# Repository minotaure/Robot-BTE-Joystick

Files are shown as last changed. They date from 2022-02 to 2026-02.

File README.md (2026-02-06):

# Robot-BTE-Joystick
Robot Mélia de découverte pour l'Ecole des Mines de Paris et classes de 3ème

## Participants au projet (ordre alphabétique):
Maxime CHUREAU\
Remy MARTINEZ\
Naimeric VILLAFRUELA

## Versions des robots
2 versions sont disponibles :
* Une version du robot contrôlable via une interface WEB via du WIFI (robot-version-wifi)
* Une autre contrôlable via un joystick Bluetooth (robot-version-BT)

## Les fichiers

- BOM (contient les listes de matériels pour fabriquer les robots)

- robot-version-BT (contient la bersion Bluetooth)
    - Code (contient le code pour le robot et la télécomande)
    - Electronique (contient le schéma fritzing et un jpg du schéma)

[Attention : La version robot-version-BT n'est pas complètement fonctionnelle. Seule la version contenue dans robot-v-finale est fonctionnelle]
    
- robot-version-wifi (contient la version Wifi)

- Structure (contient les fichiers de la structure du robot (identique pour les deux))
    - STLs (contient les pièces à imprimer pour sur-élever la bille avant et fixer les moteurs)
    - SVGs (contient le schéma de la plateforme à découper au laser)

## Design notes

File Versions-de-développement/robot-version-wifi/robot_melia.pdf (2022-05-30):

# Le robot Mélia

### Rémy Martinez - Cahier Vert 2022

## Table des matières

1 Introduction | 2
2 Le robot | 2
3 Montage | 2
4 Pistes d’amélioration | 5

1

## 1 Introduction

Le montage du robot est une des activités proposées par le pôle Mélia de Cahier Vert. L’idée est de permettre une introduction de problématiques d’ingéniérie auprès d’élèves de 3e au travers du montage d’un petit robot. Ce document vise à être une sorte de mode d’emploi complet des fonctionnalités du robot et de son montage (à l’issue du mandat 2021-2022).

## 2 Le robot

Le robot étant un support pédagogique adressé aux collégiens, il doit attirer leur attention tout en étant "sobre" d’un point de vue du matériel. Le choix a donc été fait de concevoir un robot roulant, avec deux roues motrices et une roue libre. Le tout se base sur une architecture composée d’un arduino et d’un hacheur.

## 3 Montage

### 3.1 Le matériel

### 3.1.1 L’arduino

Le design retenu en 2022 se base sur un arduino nano capable d’être l’hote d’un réseau wifi. Plusieurs modèles peuvent faire l’affaite : nano iot 33, bte, ou RP2040. De par les capteurs pré-intégrés (accéléromètre, LED RGB, micro ...) et dans une optique de futures améliorations nous avons choisi les RP2040. Il en faut un par robot et c’est lui qui gère toute la partie commande.
[insérer image d’un arduino]
Attention : Il peut être alimenté via du micro USB ou directement sur le pin VIN (allez voir dans la doc lequel c’est, ce pin est assez tolérant en termes de tensions qu’il accepte). Cependant il est fortement déconseillé de l’alimenter par ces deux voies en même temps : il risque de griller. Attention 2 : Contrairement aux arduino "classiques" pour lesquels les niveaux logiques sont 0 et 5V, pour les arduino nano c’est 0 et 3.3V. Faites attention a être cohérent dans un même circuit pour ne pas avoir de mauvaises surprises

2

### 3.1.2 Le hacheur

Nous avons cherché un hacheur qui peut faire varier la tension (pour faire tourner les moteurs a différentes vitesses), avec 2 canaux (un par roue), qui prenne une tension logique 3.3V et qui soit le moins cher possible. Nous avons donc convergé vers les L9110 de Kitronic.
Warning : L’alimentation des hacheurs a une polarité et ils ne sont pas forcement protégés contre un mauvais branchement. Donc branchez les bien ! [insérer image d’un hacheur]

### 3.1.3 Matériel supplémentaire

Pour un robot il faut ajouter à cela : - Du contreplaqué 5mm (2 pièces à découper au laser + des cales a découper)

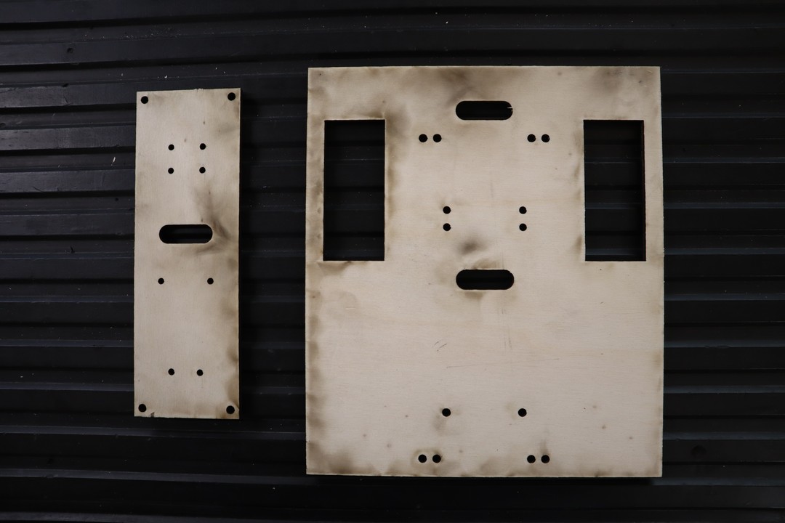
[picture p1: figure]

Figure 1 – Pièces à découper

- Deux "moteurs jaunes" + les roues qui vont avec
- Une bille porteuse (roue avant)
- une pile 9V (qui alimente la partie commande et puissance)
- une prise pour brancher sur pile 9V
- Des connecteurs JST SM mâle et femelle (3 de chaque)
- Des connecteurs de carte electronique (2 x 15 broches)
- Des vis : 8 de 15mm pour accrocher l’electronique et les equerres au châssis, 8 de 25mm pour attacher le support elec au châssis et les moteurs aux équerres, deux de 30mm (idéalement ca aurait été au moins 35mm) pour attacher la bille porteuse.
- Les écrous qui vont avec : 18 écrous
- Un bout de velcro pour coller la pile

3

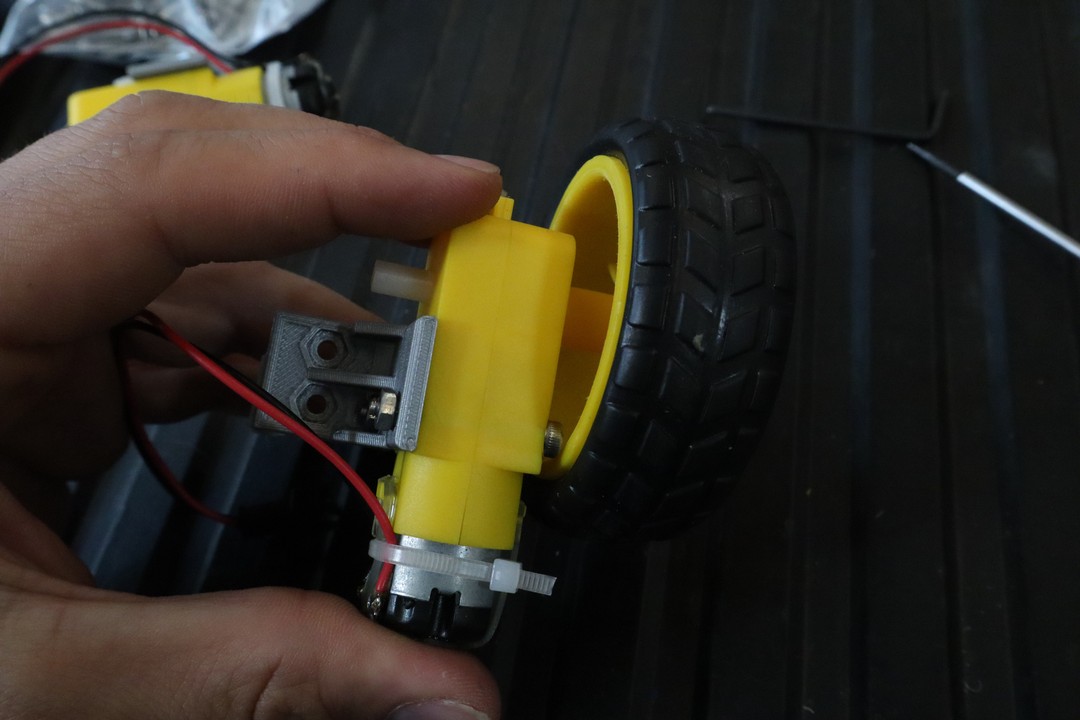
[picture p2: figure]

Figure 2 – Moteur jaune et roue (qui se rentre en force)

- Les pièces imprimées en 3D : 1 support de nano, 1 équerre gauche, 1 équerre droite
- Quelques outils

### 3.2 Instructions de montage

### 3.2.1 A faire en amont d’une session

- Découper les planches
- Soudures de l’electionique - Branchement 9V - Distribution de l’alimentation
- Fils de commande (arduino - hacheur)
- Fils en sortie du hacheur :
- Fils JST sur moteurs

### 3.2.2 Le montage

- Accorcher les moteurs sur les équerres ( Attention Equerre gauche ̸= Equerre droite)
- Accrocher l’electronique au support elec
- Accrocher Equerres sur chassis
- Accrocher bille sous chassis
- Accrocher le support elec au chassis (le faire en dernier sinon le reste ne peut plus être monté)

4

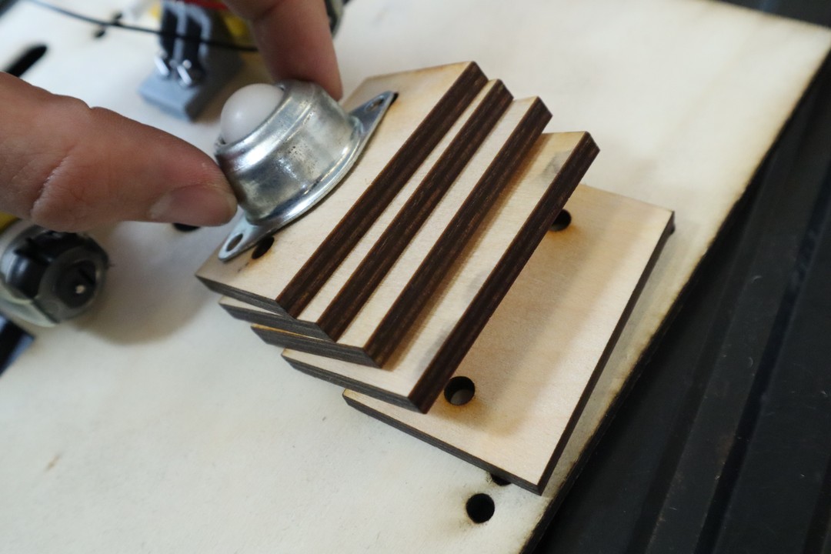
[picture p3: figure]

Figure 3 – Bille porteuse et cales

## 4 Pistes d’amélioration

- Avoir une connexion où les collégiens ne peuvent pas se planter au niveau du côté commande du hacheur
- Implémenter un joystick (il y a un code a base de websocket mais pas trouvé comment ca marche côté arduino)
- Amélioration ultime : Utiliser la centrale inertielle du RP2040 pour faire un robot en pendule inversé (faire une V2 du robot)

5

Figure 4 – Pile et velcro

Figure 5 – Support de nano imprimé en 3D

6

Figure 6 – Equerres imprimées en 3D

Figure 7 – Ecrous et clé

7

Figure 8 – Hallen et tournevis

Figure 9 – La découpe laser

8

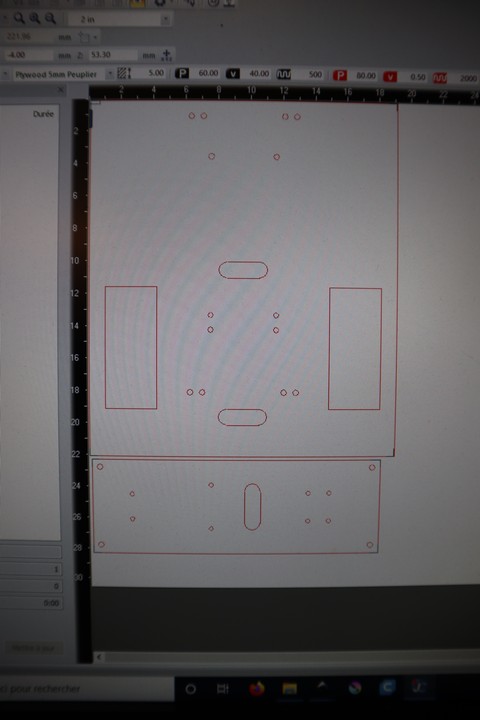
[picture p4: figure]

Figure 10 – Positionnement optimal des pièces

Figure 11 – Découpe en cours

9

Figure 12 – Fil 1 : Connexion à l’alimentation

Figure 13 – Fil 2 : Séparation en 2

10

Figure 14 – Fil 2 : Branchement des fils d’alim côté arduino

Figure 15 – Fil 2 : Zoom sur la connexion au broches de l’arduino

11

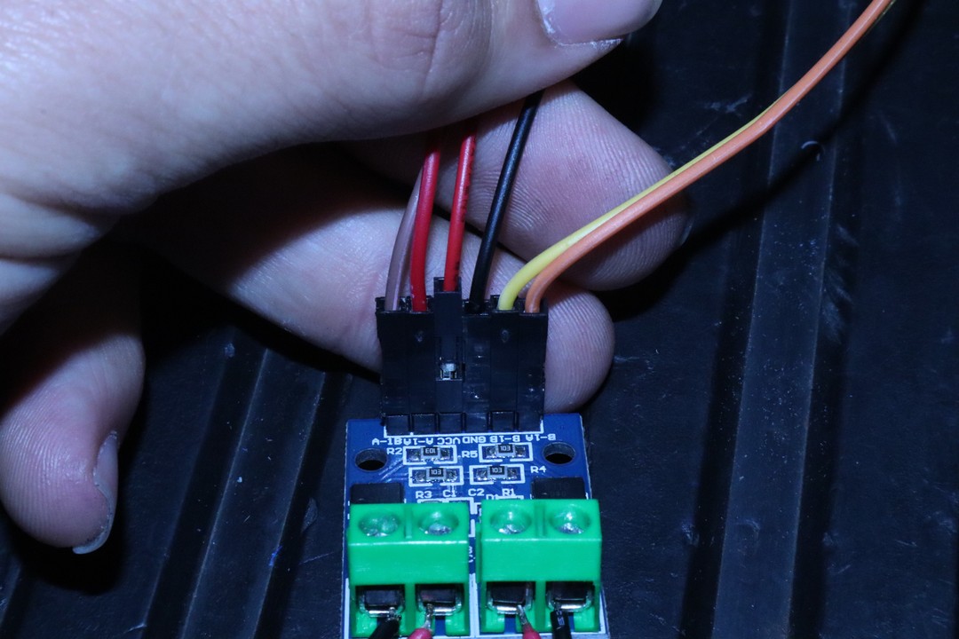
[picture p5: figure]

Figure 16 – Fil 2 : Branchement de l’alim côté hacheur (ce sont les fils rouge et noir au centre)

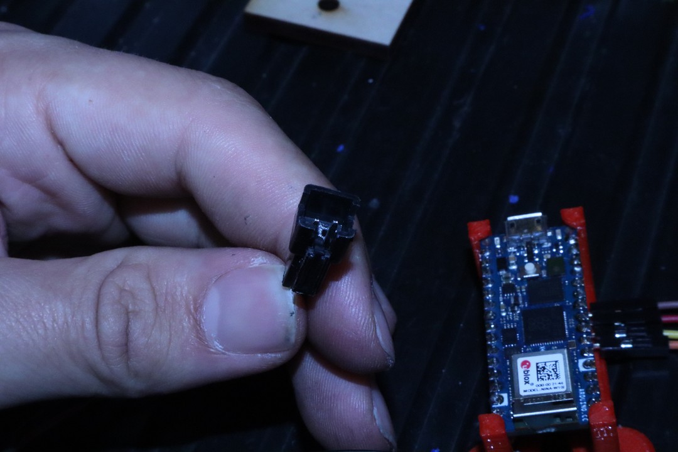
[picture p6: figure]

Figure 17 – Fil 2 : Prise JST d’alim côté arduino

12

Figure 18 – Fils 3 : Commande cpôté hacheur (les 2 fils de chaque côté)

Figure 19 – Fil 3 : Branchement de la commande côté arduino

13

Figure 20 – Fil 3 : Zoom sur la connexion aux broches de l’aduino

Figure 21 – Branchement des fils sur l’aduino (vu de dessous)

14

Figure 22 – Fils 4 : Connexion prise JST au hacheur

Figure 23 – Fils 5 : Soudure côté moteur

15

Figure 24 – Fil 5 : Prise côté moteurs

Figure 25 – Attache d’une équerre sur un moteur

16

Figure 26 – Equerres pour écrous hex.

Figure 27 – Support de l’electronique

17

Figure 28 – Moteur accroché au châssis

Figure 29 – Mise en place de la bille porteuse

18

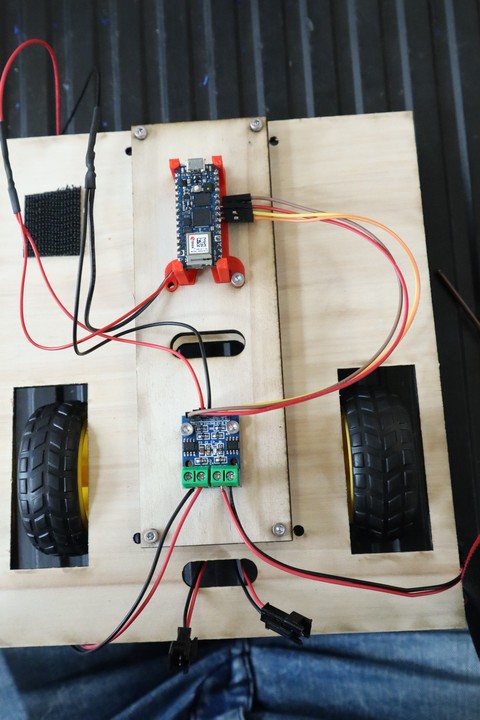
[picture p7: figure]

Figure 30 – Robot complet

19

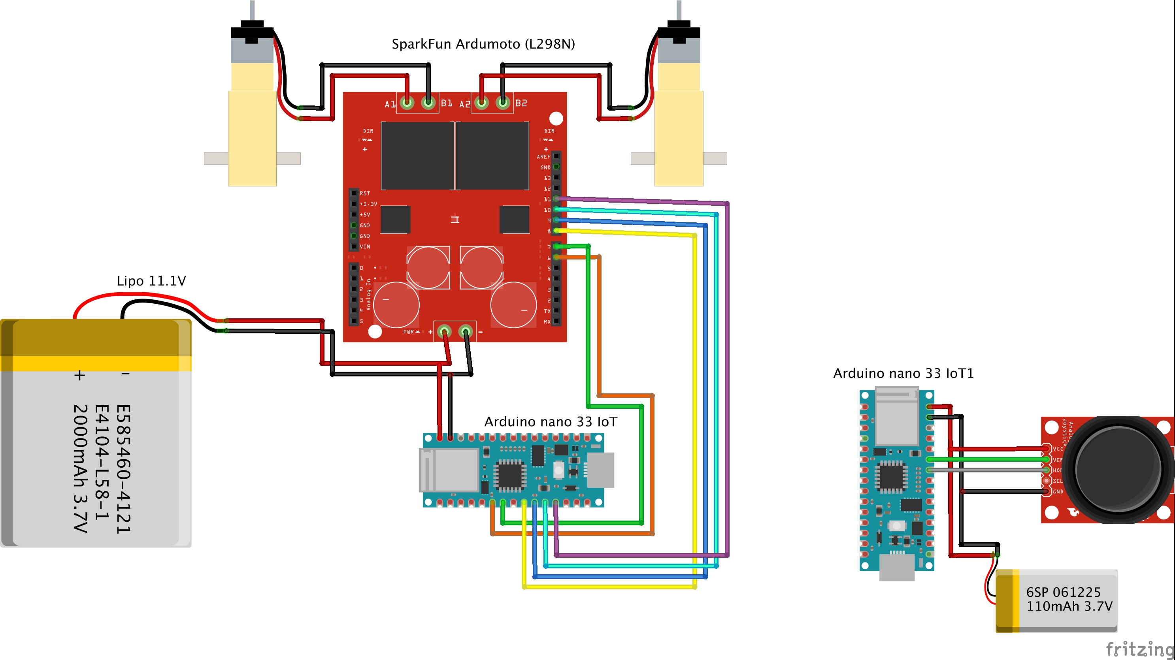
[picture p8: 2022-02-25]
Versions-de-développement/robot-version-BT/Electronique/Robot-joystick-BT.jpg

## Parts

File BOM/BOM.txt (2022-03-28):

BOM pour la version Robot + Joystick BT
##################

Arduino Nano 33 IoT : x2
Batterie Lipo 11.1V 3S : x 1
Batterie lipo 3.3V 1S : x1
Connecteur Lipo 11.1V (Femelle):  x1
Connecteur Batterie lipo 3.3V (Mµ«le+Femelle): x1
Connecteur JST 2 Pin Batterie - Arduino (Mµ«le+Femelle): x2
Connecteur JST 2 Pin Joystick - Arduino (Mµ«le+Femelle): x1
Connecteur JST 4 Pin Ardumoto-Arduino : (Mµ«le+Femelle) : x1
Moteur chinois jaunes : x2
Sparkfun Ardumoto ou identique (L298N) : x1
Joystick : x1

BOM pour la version Robot + Nano RP2040
##################

Arduino Nano RP2040 : x1
Batterie 9V 6lr61 ou Bloc Piles AA (sortie connecteur 9V) : x1
Connecteur 9V : x1
Connecteur JST SM 2 broches : x3
Connecteurs JST Femelle (pour brancher Arduino) : 2 x barres de 15 broches
Connecteurs JST Femelle (pour brancher hasheur) : 1 x barres de 6 broches
Moteur chinois jaunes : x2
Roues : x2
Carte driver moteurs 2 canaux (L9110S Kitronik) : x1
Vis CHC-M3-25 : x8 (moteur + plaque support breadboard)
Vis CHC-M4-40 : x2 (boule)
Vis CHC-M2-15 : x4 (hasheur)
Ecrous M3 : x8
Ecrous M4 : x2
Ecrous M2 : x4
Bille Porteuse : x1

Velcro autocollant
Cable ¨¦lectrique 1.5mm2 si possible de couleurs diff¨¦rentes
Piece STL pour fixer nano RP2040
(Contreplaqué 5mm)

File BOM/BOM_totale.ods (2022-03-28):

BOM pour la version Robot + Nano RP2040 |  |  |  |  |  |  |  |  |  | N | 30
 |  |  |  | Où le trouver + prix par unité |  |  |  |  |  |  |  |  |  | Prix pour N robots
 | Piècce | Qté pour 1 robot |  | RS | Prix RS | Conrad | Prix Conrad | Autre |  |  | Qté pour N robots | En stock | Qté nette à acheter | RS | Conrad | Autre
note : j’ai pris aavec les embases car a souder on a toutes les chances d’en casser au moins 1 | Arduino Nano RP2040 : x1 | 1 |  | https://fr.rs-online.com/web/p/arduino/2221486 | 27,80 € |  | 32,00 € |  |  |  | 30 | 0 | 30 | 834,00 € | 960,00 € | 0
 | Batterie 9V 6lr61 + connecteur 9V ou Bloc Piles AA avec connecteur 9V : x1 | 1 | conrad est moins cher pour les piles 9v |  |  | https://www.conrad.fr/p/emmerich-industrial-6lr61-pile-6lr61-9v-alcalines-500-mah-20-pcs-1662617 | 1,00 € |  |  |  | 30 | 0 | 30 | 0,00 € | 30,00 € | 0
 | Connecteur pour 9V | 1 |  |  | 1,00 € | https://www.conrad.fr/p/connecteur-clip-pression-1x-6lr61-9-v-beltrona-9v-i-clip-raccordement-par-empreinte-pile-9v-l-x-l-x-h-26-x-13-x-8-mm-624691 | 0,92 € |  |  |  | 30 | 25 | 5 | 5,00 € | 4,60 € | 0
 | Connecteur JST SM 2 broches : x3 | 3 |  |  |  |  |  | https://www.amazon.fr/GTIWUNG-Connector-Adaptateur-Connecteur-%C3%89lectrique/dp/B07VYTHHHL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 | 0,4495 |  | 90 |  | 90 | 0 | 0 | 40,455
note on ne met qu’une barre de 36 broches | Connecteurs JST Femelle (pour brancher Arduino) barres de 15 broches | 1 | (barre de 36) | https://fr.rs-online.com/web/p/connecteurs-femelles-pour-ci/1731065 | 3,00 € |  |  |  |  |  | 30 |  | 30 | 90,00 € | 0 | 0
 | Connecteurs JST Femelle (pour brancher hasheur) barres de 6 broches | 0 |  |  |  |  |  |  |  |  | 0 |  | 0 | 0 | 0 | 0
 | Moteur chinois jaunes : x2 | 2 |  |  |  |  |  | https://www.amazon.fr/Gebildet-DC3V-6V-Voiture-motrices-robotique/dp/B08D39MFN1 | 1,80 € |  | 60 | 44 | 16 | 0 | 0 | 28,80 €
 | Roues : x2 | 2 |  |  |  |  |  | kit avec moteurs | 1,80 € |  | 60 | 40 | 20 | 0 | 0 | 36,00 €
 | Carte driver moteurs 2 canaux (L9110S Kitronik) : x1 | 1 |  | https://fr.rs-online.com/web/p/complements-bbc-micro-bit/2153182/?searchHistory=%7B%22enabled%22%3Atrue%7D | 1,00 € |  |  |  |  |  | 30 |  | 30 | 30,00 € | 0 | 0
 | Vis CHC-M3-25 : x8 (moteur + plaque support breadboard) | 8 |  |  |  |  |  |  |  |  | 240 |  | 240 | 0 | 0 | 0
 | Vis CHC-M4-40 : x2 (boule) | 2 |  |  |  |  |  |  |  |  | 60 |  | 60 | 0 | 0 | 0
 | Vis CHC-M2-15 : x4 (hasheur) | 4 |  |  |  |  |  |  |  |  | 120 |  | 120 | 0 | 0 | 0
 | Ecrous M3 : x10 | 10 |  |  |  |  |  |  |  |  | 300 |  | 300 | 0 | 0 | 0
 | Ecrous M2 : x4 | 4 |  |  |  |  |  |  |  |  | 120 |  | 120 | 0 | 0 | 0
 | Ecrous M4 : x2 | 2 |  |  |  |  |  |  |  |  | 60 |  | 60 | 0 | 0 | 0
 | Bille Porteuse | 1 |  |  | 5,00 € | Passer par amazon carbcp moins cher |  | https://www.amazon.fr/WEKON-Transfert-Roulettes-Inf%C3%A9rieure-Roulement/dp/B083FSLM8Z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 | 1,665 |  | 30 | 11 | 19 | 95,00 € | 0 | 31,635
 |  |  |  |  |  |  |  |  |  |  |  |  |  | 0 | 0 | 0
 | Piece STL pour fixer nano RP2040 | 1 |  |  |  |  |  |  |  |  | 30 |  | 30 | 0 | 0 | 0
 | Cable ¨¦lectrique 1.5mm2 si possible de couleurs diff¨¦rentes |  |  |  |  |  |  |  |  |  | 0 |  | 0 | 0 | 0 | 0
note, il faut deux tiers pour un robot | Velcro autocollant | 2 |  |  |  |  |  | https://www.amazon.fr/3550-Dual-fermeture-pression-connexions-Reversible/dp/B06XR1Q9GG?s=hi | 0,333333333333333 |  | 60 |  | 60 | 0 | 0 | 20
 | (Contreplaqué 5mm) |  |  |  |  |  |  |  |  |  | 0 |  | 0 | 0 | 0 | 0

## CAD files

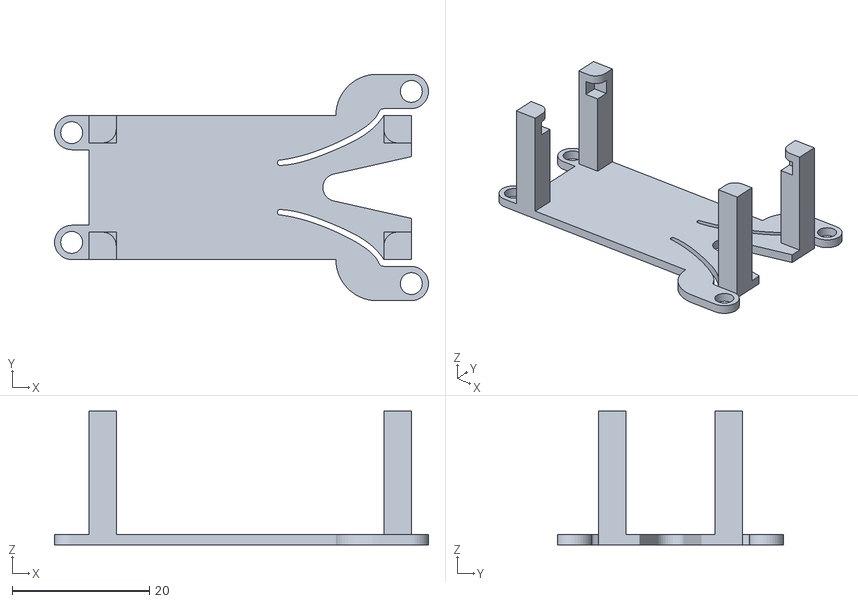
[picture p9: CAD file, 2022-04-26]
Structure/STLs/Support nano v4.stl
54.5 x 33.0 x 19.5

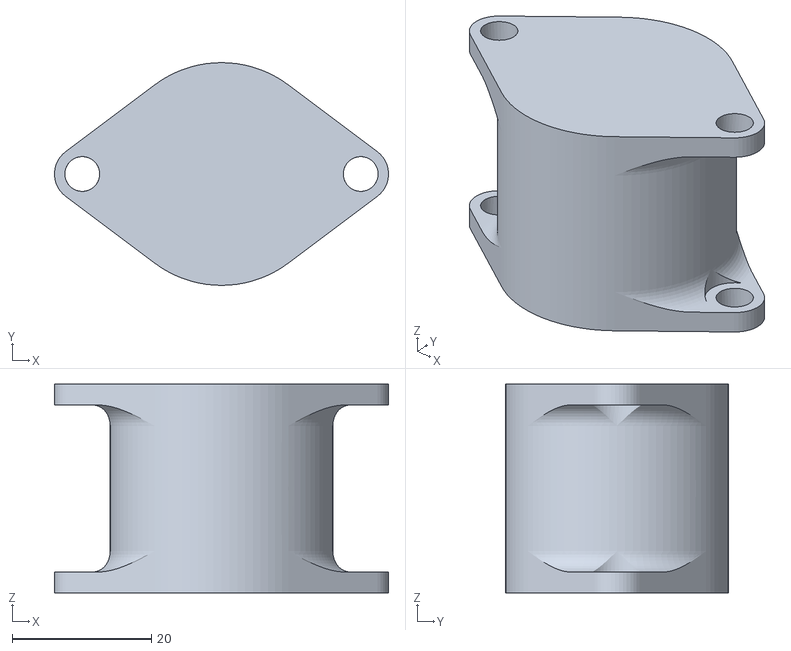
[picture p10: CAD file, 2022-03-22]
Structure/STLs/Ball-support.stl
48.0 x 32.0 x 30.0

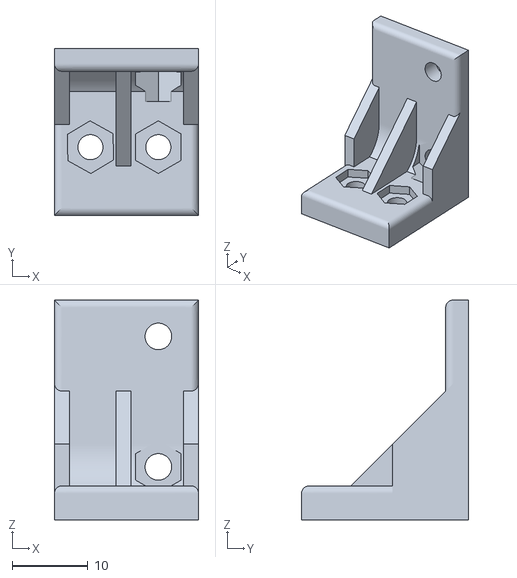
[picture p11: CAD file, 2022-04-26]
Structure/STLs/Right-motor-bracket-hex-nut.stl
19.0 x 22.0 x 29.0

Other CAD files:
Structure/STLs/Left-motor-bracket-hex-nut.stl
Structure/STLs/Right-motor-bracket-sq-nut.stl
Structure/STLs/Left-motor-bracket-sq-nut.stl

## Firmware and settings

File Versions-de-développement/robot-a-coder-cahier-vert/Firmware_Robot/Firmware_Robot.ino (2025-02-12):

/*
  Logiciel embarqué du robot de formation Minotaure.
  Crée un point d'accès wifi et héberge un serveur http qui contrôle les roues.
  Conçu pour Arduino Nano RP2040 Connect.

  Auteur : Léopold Gravier - Assocation Minotaure - Mines Paris PSL

  Crée à partir du code de : Rémy Martinez - Pole Mélia Cahier Vert - Mines ParisTech 2022
  Pour le robot Mélia (https://github.com/minotaure/Robot-BTE-Joystick)  

  Code modifié par Romain TEISSANDIER pour un autre atelier Cahier Vert
*/


// ------- Libraries -------
#include <WiFiNINA.h> // Library for wifi communication
#include <SPI.h>
#include <ArduinoJson.h>    // Library to read JSON documents

#include "HttpRequest.h"    // Code to parse HTTP requests

// Data
#include "main_html.h"       // The web page data
#include "arduino_secrets.h" // Contains SSID and Password for the wifi


// ------- Variables -------

// --- WiFi ---
char ssid[] = SECRET_SSID;        // your network SSID (name)
char pass[] = SECRET_PASS;    // your network password (use for WPA, or use as key for WEP)
int keyIndex = 0;                // your network key index number (needed only for WEP)

int wifi_status = WL_IDLE_STATUS;

// --- Web server ---
WiFiServer http_server(80);
char html_page[] = HTML_CODE;

// --- Pins ---
// Left motor
const int MOTOR_PIN_LEFT_PLUS = 9;
const int MOTOR_PIN_LEFT_MINUS = 8;
// Right motor
const int MOTOR_PIN_RIGHT_PLUS = 7;
const int MOTOR_PIN_RIGHT_MINUS = 6;

// Nombre d'exécutions d'une boucle

int execution_count = 0;


// ------- Main functions -------

// Called once when the program starts
void setup() {
  // --- Partie LED ---
  SetupLed();
  SetLedColor(255, 255, 0); // Set the embedded LED to yellow to indicate that the robot is booting up

  // --- Partie USB ---
  //Initialize serial and wait for port to open:
  Serial.begin(115200);
  
  // Wait up to 5s for the connection to establish (it is important if we want to receive the first messages)
  unsigned long timeout_date = millis() + 5000;
  while (!Serial && millis() < timeout_date) {
    delay(10);
  }

  // --- Partie Wifi ---
  
  Serial.println("Creating access Point Web Server");

  // Start the WiFi access point
  SetupWiFi();
  // Start the web server on port 80
  http_server.begin();

  PrintWiFiInfo();

  SetLedColor(0, 0, 255); // Set the embedded LED to blue to indicate that the robot is waiting for a connection

  // --- Partie Robot ---
  pinMode(MOTOR_PIN_LEFT_PLUS, OUTPUT);
  pinMode(MOTOR_PIN_LEFT_MINUS, OUTPUT);
  pinMode(MOTOR_PIN_RIGHT_PLUS, OUTPUT);
  pinMode(MOTOR_PIN_RIGHT_MINUS, OUTPUT);

  analogWrite(MOTOR_PIN_LEFT_PLUS, 0);
  analogWrite(MOTOR_PIN_LEFT_MINUS, 0);
  analogWrite(MOTOR_PIN_RIGHT_PLUS, 0);
  analogWrite(MOTOR_PIN_RIGHT_MINUS, 0);
}


// Called repeatedly
void loop() {

  if (execution_count == 0){
    // Exercice 1

    SetMotorsVelocity(255, 255);  // On fait tourner les moteurs à pleine puissance
    delay(10000);  // On attend 10 sec
    SetMotorsVelocity(0, 0);  // On arrête les moteurs
    execution_count = 1;

    // Exercice 2

    // **** à compléter ****

    // auto v =
    // auto b =

    // ****

    // SetMotorsVelocity(b, b);
    // delay(8000);
    // SetMotorsVelocity(0, 0);
    // execution_count = 1;

    // Exercice 3

    // for (int i = 0; i < 1000; i++){
    //   int t = i * 10;  // conversion pour avoir un temps en ms

      // **** à compléter ****

      // auto v =
      // auto b =

      // ****

      // On vérifie que la vitesse de rotation 
      
      // if (b > 255){
      //   b = 255;
      // }

      // SetMotorsVelocity(b, b);
      // delay(10);
    // }

    // SetMotorsVelocity(0, 0);
    // execution_count = 1;
  }
}


// ------- Movement functions -------

void SetRobotVelocity (int forward, int right) {
/* Set the velocity of the robot
  -255 <= forward <= 255   ->   Velocity on the forward/backward axis
  -255 <= right <= 255     ->   Velocity of the left/right axis
  */

  int leftMotorRaw = forward + right;
  int rightMotorRaw = forward - right;

  int maxMotorInput = max(abs(leftMotorRaw), abs(rightMotorRaw));
  float normFact = min(1.0, 255.0 / maxMotorInput);

  SetMotorsVelocity(leftMotorRaw * normFact, rightMotorRaw * normFact);
}


void SetMotorsVelocity (int _left, int _right) {
/* Set the velocity of the two motors
  -255 <= left <= 255    ->   Velocity of the left motor
  -255 <= right <= 255   ->  Rotation speed
  */

  Serial.println("(" + String(_left) + ", " + String(_right) + ")");

  int left = -_left;
  int right = -_right;

  // Manage left motor
  if (left >= 0) {
    analogWrite(MOTOR_PIN_LEFT_PLUS, left);
    analogWrite(MOTOR_PIN_LEFT_MINUS, 0);
  } else {
    analogWrite(MOTOR_PIN_LEFT_PLUS, 0);
    analogWrite(MOTOR_PIN_LEFT_MINUS, -left);
  }

  // Manage right motor
  if (right >= 0) {
    analogWrite(MOTOR_PIN_RIGHT_PLUS, right);
    analogWrite(MOTOR_PIN_RIGHT_MINUS, 0);
  } else {
    analogWrite(MOTOR_PIN_RIGHT_PLUS, 0);
    analogWrite(MOTOR_PIN_RIGHT_MINUS, -right);
  }
}

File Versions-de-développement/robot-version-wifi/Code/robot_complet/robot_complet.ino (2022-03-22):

/*

  Créé à partir de : "  Commande REGO (Robot de téléprésence)
  by Franck DE WIT <http://www.lelabtechno.com>
  Twitter : @fdw34
  Programme pour Arduino nano RP2040 Connect
  27/08/2021"

  Rémy Martinez - Pole Mélia Cahier Vert - Mines ParisTech 2022
*/
///////////////////////////////////////////////////////////////////////////////////////////////////Partie Wifi
#include <SPI.h>
#include <WiFiNINA.h> //Library for wifi communication
#include "arduino_secrets.h" //Contains SSID and Password
#include "web_interface.h" //Le code correspondant au site internet
#include <Wire.h>

///////please enter your sensitive data in the Secret tab/arduino_secrets.h
char ssid[] = SECRET_SSID;        // your network SSID (name)
char pass[] = SECRET_PASS;    // your network password (use for WPA, or use as key for WEP)
char html[] = HTML_CODE;
int keyIndex = 0;                // your network key index number (needed only for WEP)

int led =  LED_BUILTIN;
int status = WL_IDLE_STATUS;
WiFiServer server(80);

///////////////////////////////////////////////////////////////////////////////////////////////////Partie Robot

#define A1 9  // Motor A pins
#define A2 8
#define B1 7 // Motor B pins
#define B2 6


void Avant();
void Recule();
void Gauche();
void Droite();
void stopMotor();

void setup() {
  ////////////////////////////////////////////////////////////////Partie Wifi
  //Initialize serial and wait for port to open:
  Serial.begin(9600);

  Serial.println("Access Point Web Server");

  pinMode(led, OUTPUT);      // set the LED pin mode

  // check for the WiFi module:
  if (WiFi.status() == WL_NO_MODULE) {
    Serial.println("Communication with WiFi module failed!");
    // don't continue
    while (true);
  }

  String fv = WiFi.firmwareVersion();
  if (fv < WIFI_FIRMWARE_LATEST_VERSION) {
    Serial.println("Please upgrade the firmware");
  }

  // by default the local IP address will be 192.168.4.1
  // you can override it with the fol0ing:
  WiFi.config(IPAddress(192, 168, 2, 2));

  // print the network name (SSID);
  Serial.print("Creating access point named: ");
  Serial.println(ssid);

  // Create open network. Change this line if you want to create an WEP network:
  status = WiFi.beginAP(ssid, pass);
  if (status != WL_AP_LISTENING) {
    Serial.println("Creating access point failed");
    // don't continue
    while (true);
  }
  {
    // wait 10 seconds for connection:
    delay(10000);

    // start the web server on port 80
    server.begin();

    // you're connected now, so print out the status
    void printWiFiStatus();
  }
  ///////////////////////////////////////////////////////////////////////Partie Robot
  {
  pinMode(A1, OUTPUT);
  pinMode(A2, OUTPUT);
  pinMode(B1, OUTPUT);
  pinMode(B2, OUTPUT);

  analogWrite(A1, 0);
  analogWrite(A2, 0);
  analogWrite(B1, 0);
  analogWrite(B2, 0);
  }
}


void loop() {
  ///////////////////////////////////////////////////////////////////////////////////////////Partie Wifi
  // compare the previous status to the current status
  if (status != WiFi.status()) {
    // it has changed update the variable
    status = WiFi.status();

    if (status == WL_AP_CONNECTED) {
      // a device has connected to the AP
      Serial.println("Device connected to AP");
    } else {
      // a device has disconnected from the AP, and we are back in listening mode
      Serial.println("Device disconnected from AP");
    }
  }

  WiFiClient client = server.available();   // listen for incoming clients

  if (client) {                             // if you get a client,
    Serial.println("new client");           // print a message out the serial port
    String currentLine = "";                // make a String to hold incoming data from the client
    while (client.connected()) {            // loop while the client's connected
      delayMicroseconds(30);                // This is required for the Arduino Nano RP2040 Connect - otherwise it will loop so fast that SPI will never be served.
      if (client.available()) {             // if there's bytes to read from the client,
        char c = client.read();             // read a byte, then
        Serial.write(c);                    // print it out the serial monitor
        if (c == '\n') {                    // if the byte is a newline character

          // if the current line is blank, you got two newline characters in a row.
          // that's the end of the client HTTP request, so send a response:
          if (currentLine.length() == 0) {
            // HTTP headers always start with a response code (e.g. HTTP/1.1 200 OK)
            // and a content-type so the client knows what's coming, then a blank line:
            client.println("HTTP/1.1 200 OK");
            client.println("Content-type:text/html");
            client.println();

            // the content of the HTTP response follows the header:
            client.print(html);




            // The HTTP response ends with another blank line:
            client.println();
            // break out of the while loop:
            break;
          }
          else {      // if you got a newline, then clear currentLine:
            currentLine = "";
          }
        }
        else if (c != '\r') {    // if you got anything else but a carriage return character,
          currentLine += c;      // add it to the end of the currentLine
        }

        // Check to see if the client request was "GET /A" or R or D or G or S:
        if (currentLine.endsWith("GET /A")) {
          Avant();               // GET /A Avance
        }
        if (currentLine.endsWith("GET /R")) {
          Recule();                // GET /R Recule
        }
        if (currentLine.endsWith("GET /D")) {
          Droite();                // GET /D Droite
        }


        if (currentLine.endsWith("GET /G")) {
          Gauche();                // GET /G Gauche
        }


        if (currentLine.endsWith("GET /S")) {
          stopMotor();                // GET /S Stop
        }
      }
    }

    // close the connection:
    client.stop();
    Serial.println("client disconnected");
  }
}



///////////////////////////////////////////////////////////////////////////////////////////////////////////Partie Wifi
void printWiFiStatus() {
  // print the SSID of the network you're attached to:
  Serial.print("SSID: ");
  Serial.println(WiFi.SSID());

  // print your WiFi shield's IP address:
  IPAddress ip = WiFi.localIP();
  Serial.print("IP Address: ");
  Serial.println(ip);

  // print where to go in a browser:
  Serial.print("To see this page in action, open a browser to http://");
  Serial.println(ip);

}

////////////////////////////////////////////////////////////////////////////////////////////////////Partie Robot
void Gauche()
{ // Function tourne à gauche
  Serial.println("Gauche");
  analogWrite(A1, 0);
  analogWrite(A2, 255);
  analogWrite(B1, 255);
  analogWrite(B2, 0);
}
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

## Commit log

2022-02-25 Initialisation du projet
    Plan de construction, schéma electronique, code robot et télécommande, plan découpe laser et BOM
    [schema-robot.fzz]
2022-03-03 Ajout des equerres pour moteur
    Ajout des fichiers STL des equerres moteur.
    Modif Readme.md
    [Motor-L.stl, Motor-R.stl]
2022-03-05 code pour interface wifi
    [Motor-L.stl, Motor-R.stl]
2022-03-22 Exclude Mac indexation files
    [Ball-support.stl]
2022-03-22 mise à jour BOM
    Pour version arduino RP2040
2022-03-22 Mise à jour BOM
    connecteur 6 proches et non 5 sur Hasheur
2022-03-23 BOM excel + correction bille porteuse
    [BOM_totale.ods]
2022-03-25 BOM qui avnance
    [BOM_totale.ods]
2022-03-28 Liste du matériel
    [BOM_totale.ods]
2022-04-03 Correction doublon répertoire
    Déplacment du fichier ball-support + supression du repertoire "structue"
    [Ball-support.stl]
2022-04-07 Restructuration du répertoire
    Changement dans l'organisation des fichiers et maj de readme pour expliquer la structure
    [BOM_totale.ods, schema-robot.fzz]
2022-04-18 Fichier bonne verison
    [Ball-support.stl, Motor-L.stl, Motor-R.stl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]
2022-04-26 maj montures moteur
    Mise à jour des montures moteur avec 2 versions (une pour écrous héxagonaux, une pour écrous carrés)
    [Left-motor-bracket-hex-nut.stl, Left-motor-bracket-sq-nut.stl, Motor-L.stl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]
2022-05-30 doc + codes test
    [Motor-L.stl, Motor-R.stl, Support nano v4.stl]
2022-06-01 ajout des cales bille porteuse
    [Motor-L.stl, Motor-R.stl, Support nano v4.stl]
2025-02-06 Version Finale
    La version finale est pilotée par le "Big Red Button" et comporte l'indicateur lumineux sur la carte de l'état de connexion au réseau
2025-02-12 Commentaire des bonnes parties pour les collégiens
2026-02-06 Update README.md
    Précision sur la version fonctionnelle
2026-02-06 MAJ organisation des répertoires
    Modification de la structure du repository
    [schema-robot.fzz]
